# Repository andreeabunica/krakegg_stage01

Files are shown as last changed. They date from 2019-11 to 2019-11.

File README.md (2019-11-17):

# krakegg_stage01
Krakegg is a soft robotics end effector exploring the implementation of bionic actuation for soft robotics grippers. The repository is documenting the first stage of development. 

The repository contains the files, code & hardware components used in the first prototype of the project.

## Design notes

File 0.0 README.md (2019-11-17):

# krakegg_stage01
Krakegg is a soft robotics end effector exploring the implementation of bionic actuation for soft robotics grippers. The repository is documenting the first stage of development. 

The repository contains the files, code & hardware components used in the first prototype of the project. 

In the documents, you will find: 

  A. Text instructions: 

0.Concept & process: explaining the overall process leading to the development of the Stage 1 Prototype for the soft robotics gripper. 

0_01: Bill of materials: a list of the materials used for the production for the Stage 1 Prototype, with affiliated links to similar products that can be purchased from Amazon/ local retailers. 

0_02: Build process: documenting the steps taken in order to build the Stage 1 Prototype

  B. 3D printing files: 

01_Krakegg Stage 01- Moulds_Baked (...): Rhino file of the specific moulds used for the production of the prototype

01_Krakegg Stage 01: Moulds_Parametric (...) : Grasshopper file of the parametrized moulds, in order to quickly change the parameters and generate new 3D printing-ready files 

02_Krakegg Stage 01- Connection to robot arm (...): Rhino file of the current iteration of the connection plate, air chamber and finger holder to the plate

  C. Circuit: 

03_Krakegg Stage 01- Circuit: zipped folder containing hardware circuit information, including wiring instructions

03_Krakegg Stage 01- Arduino code: .ino file containing the current iteration of Arduino code

Prototype demonstration videos: 

- Egg picking demonstration: https://www.youtube.com/watch?v=kh5d-S89E1A&feature=youtu.be

- Force sensor test: https://www.youtube.com/watch?v=OoQZakSipXg&feature=emb_title

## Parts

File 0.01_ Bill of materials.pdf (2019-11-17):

KRAKEGG / Stage 01 Final Prototype Bill of Materials

### 01. SOFT ROBOTICS FINGERS

_3D printed moulds
_casting silicone (Eco-Flex 00-50): https://www.amazon.com/Smooth-Ecoflex-00-50-Platinum-Silicone/dp/B00GJ80HIC_syringe + needle

### 02. CONNECTION TO ROBOTIC ARM

_3D printed connection plate
_bolts
_screws & nuts
_Connector rivets

### 03. HARDWARE

Connection to the robot ( to ABB 140 in this case):
_microcontroller (arduino uno or similar): https://www.amazon.com/RoboGets-Compatible-ATmega328P-Microcontroller-Electronics/dp/B 01N4LP86I (https://www.amazon.com/RoboGets-Compatible-ATmega328P-Microcontroller-Electronics/dp/B01N4LP86I)
_octocoupler:
https://www.amazon.com/Converter-Optocoupler-Isolator-Maluokasa-DST-1R4P-N/dp/B07NNP 4H7S (https://www.amazon.com/Converter-Optocoupler-Isolator-Maluokasa-DST-1R4P-N/dp/B07NNP4H7S/)
_relay:
https://www.amazon.com/Nilight-Automotive-Harness-Interlocking-Socket/dp/B0748F1JK4

Control air pressure:
_2 way solenoid valve:
https://www.amazon.com/4inch-Normally-Closed-Electric-Solenoid/dp/B00ON8XFSO_air compressor:
https://www.amazon.com/AstroAI-Portable-Compressor-Inflator-Protection/dp/B078LYX5YF_force touch sensor:
https://www.amazon.com/Sensitive-Resistor-Pressure-Diameter-Resistance-Type/dp/B07MP4R L9Q (https://www.amazon.com/Sensitive-Resistor-Pressure-Diameter-Resistance-Type/dp/B07MP4RL9Q)

General:
_jumper cables & jumper extension wires: https://www.amazon.com/Elegoo-EL-CP-004-Multicolored-Breadboard-arduino/dp/B01EV70C78_breadboard:
https://www.amazon.es/Protoboard-contactos-Breadboard-prototipos-soldadura/dp/B00JGFDKBQ/ (https://www.amazon.es/Protoboard-contactos-Breadboard-prototipos-soldadura/dp/B00JGFDKBQ)

_12V power supply:
https://www.amazon.com/Switching-Universal-Regulated-Transformer-Computer/dp/B07C2WB R1L (https://www.amazon.com/Switching-Universal-Regulated-Transformer-Computer/dp/B07C2WBR1L)
_Mounting plate or Project Box

Tools:

_Soldering iron
_Wire strippers
_Tweezers
_Screwdriver
_3D printer

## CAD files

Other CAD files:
01_Krakegg Stage 01- Moulds_ Baked Soft robotics Finger.3dm
02_Krakegg Stage 01- Connection to robot arm 3D printing file.3dm

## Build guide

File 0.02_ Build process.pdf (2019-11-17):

KRAKEGG / Stage 01 Final Prototype Build process

### 01. SOFT ROBOTICS FINGERS

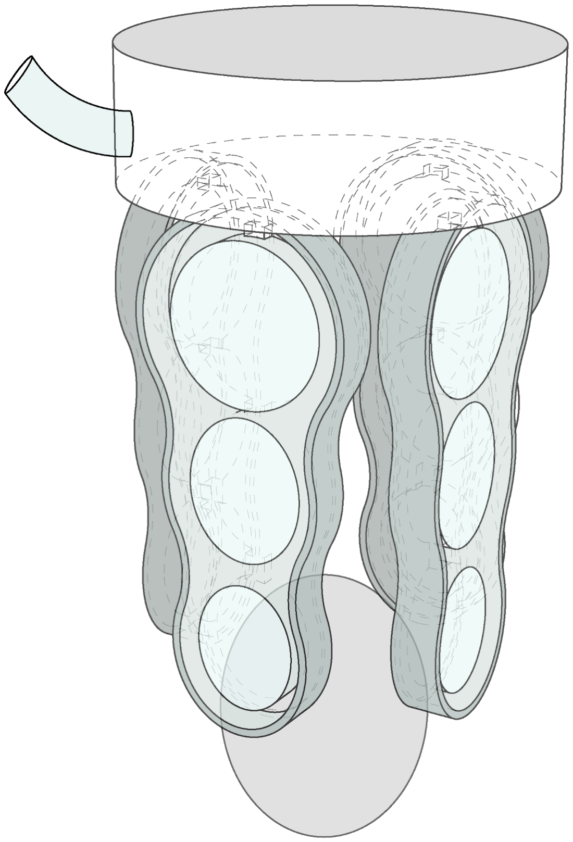
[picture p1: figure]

1. Design your mould using the attached grasshopper file, or download the 3D printing-ready files from the attached Rhino file.

Make sure to add a T-shaped end to the beginning of your air channel in order to later attach the fingers to the robot connection module.

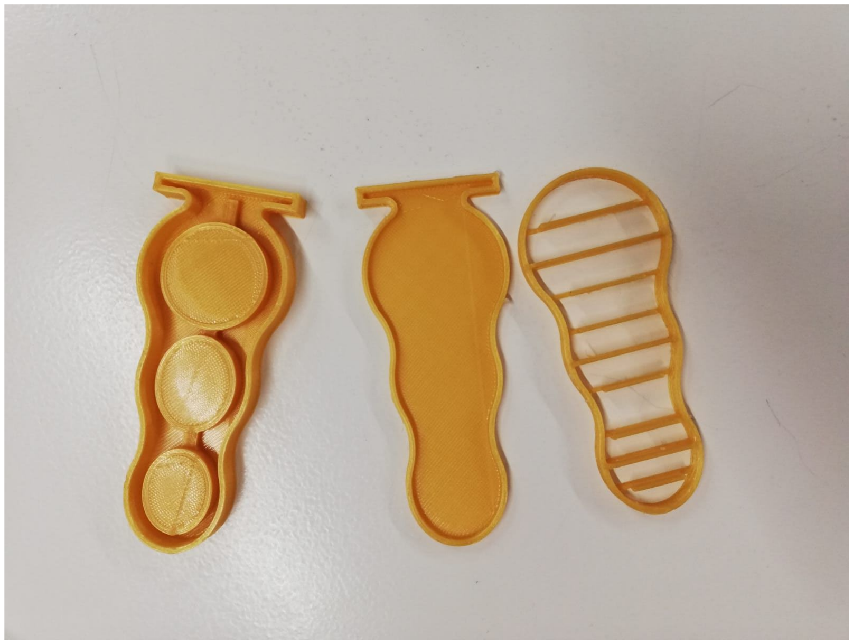
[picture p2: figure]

2. 3D print your mould (photo above)
3. Mix the two parts of Eco-flex 00-50 silicone according to the instructions on the packaging.
4. Pour the silicone in the bottom mould, up to the lip.
5. Pour the silicone in the main body mould, up to the lip. Then, place the spacer mould on top, making sure the indents are sunk in the silicone poured in the main body mould.

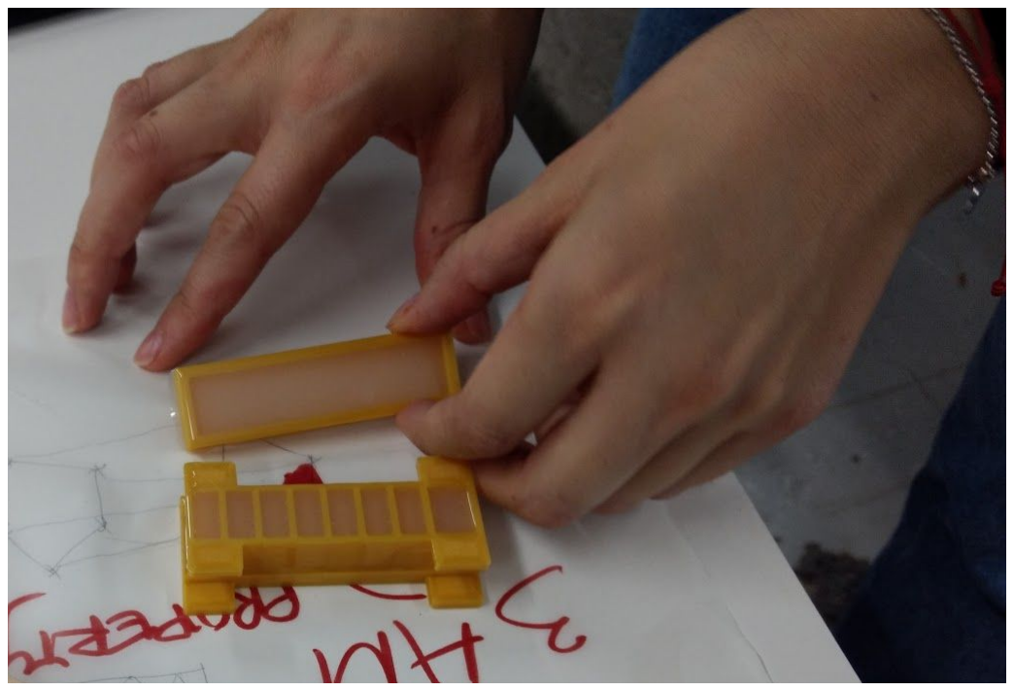
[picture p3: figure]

6. Leave the moulds to dry for at least 2 hours before carefully de-moulding.
7. Glue the bottom mould to the main body mould by applying a thin layer of silicone on the edges of the bottom mould and then placing the main body mould on top. Apply extra silicone on the vertical walls around the seam if needed to tightly close the mould.

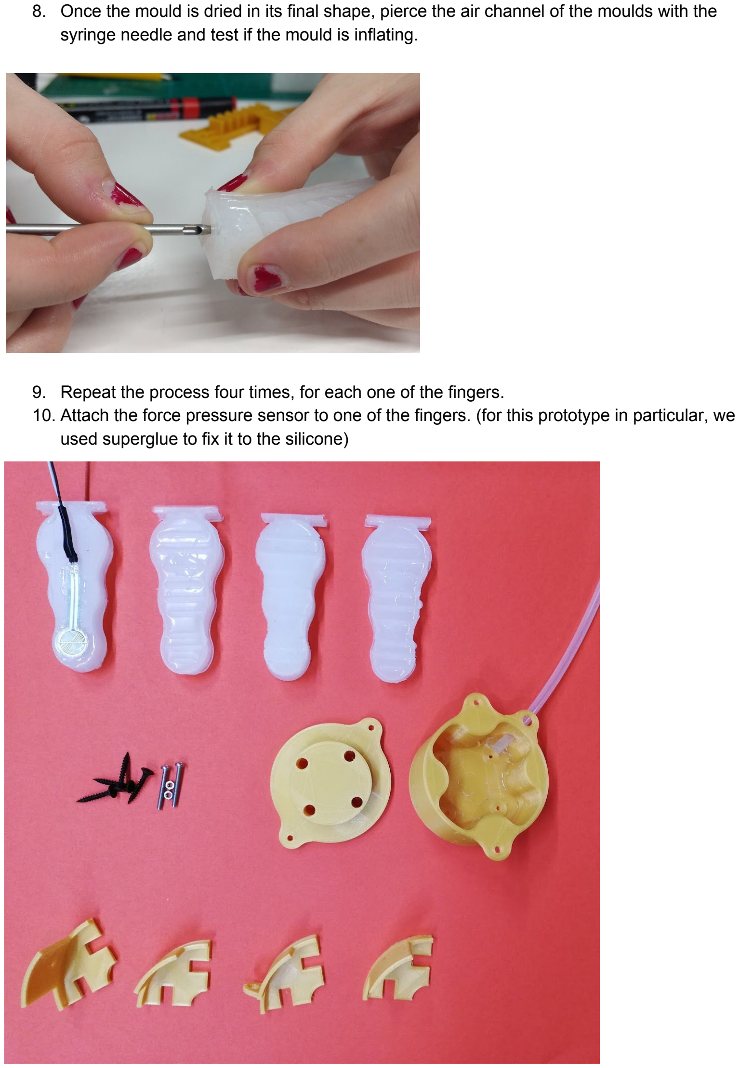
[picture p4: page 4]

8. Once the mould is dried in its final shape, pierce the air channel of the moulds with the syringe needle and test if the mould is inflating.
9. Repeat the process four times, for each one of the fingers.
10. Attach the force pressure sensor to one of the fingers. (for this prototype in particular, we used superglue to fix it to the silicone)

### 02. CONNECTION TO ROBOTIC ARM

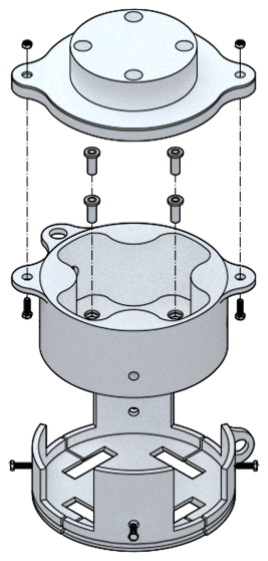
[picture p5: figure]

1. Download the Rhino file for the robot arm connection and 3D print it.
2. First screw in the robot arm connection plate using bolts compatible to the specific robot arm you are working with
3. Glue in the air inputs to the fingers to the bottom of the air chamber. (In this case we used four cut-up aluminium rivets as air inputs)
4. Fix each finger in between the finger holder plates and connect each one of them to one of the air inputs.
5. Fix the air chamber to the robot connection plate using screws and washers. (In this case we ended up cutting up a rubber plate in the shape of the connection plate and placing it in between the air chamber and the connection plate in order to reduce the amount of air leakage)
6. Fix the finger holders and the fingers to the rest of the connection module using screws.

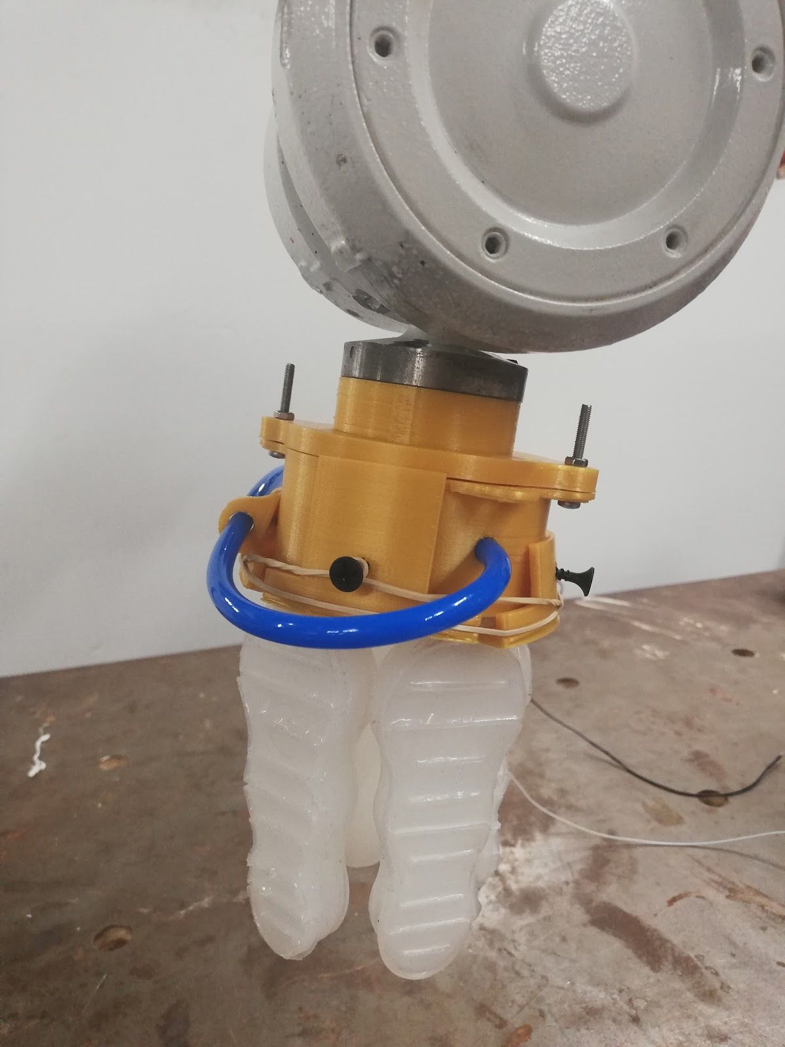
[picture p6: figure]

* This prototype
also used electrical
tape and elastic
bands as an extra
sealing layer to
reduce air leakage
to workable levels

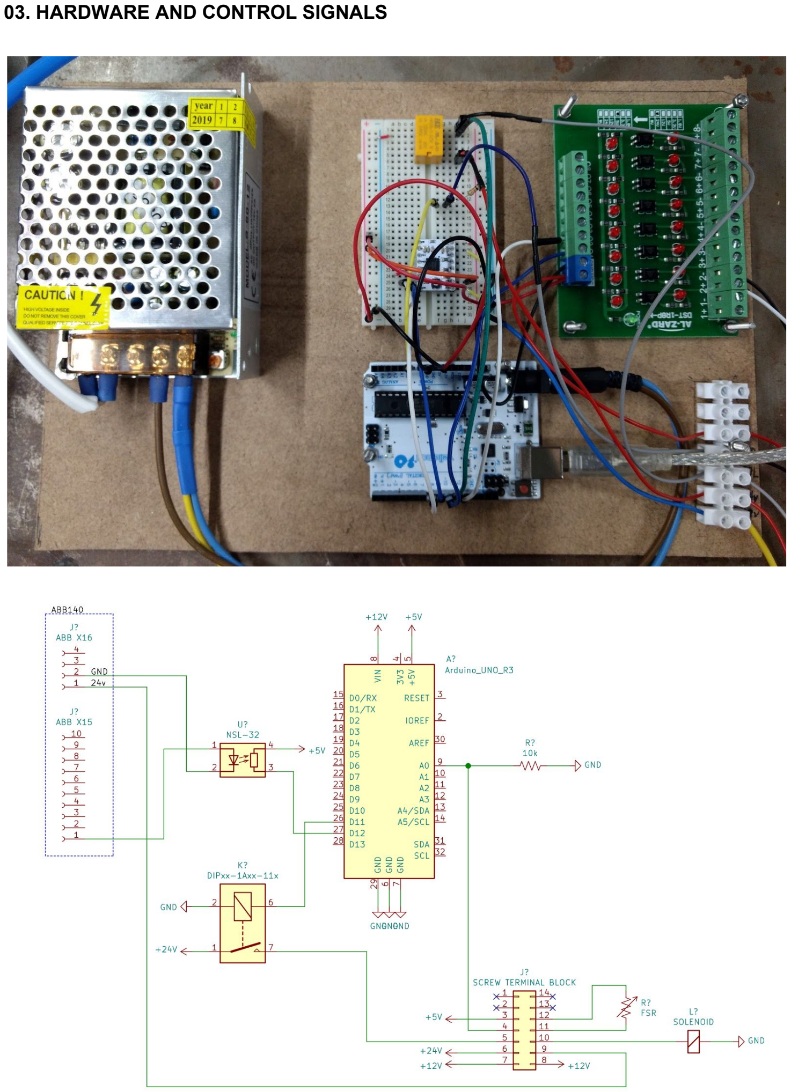
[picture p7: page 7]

### 03. HARDWARE AND CONTROL SIGNALS

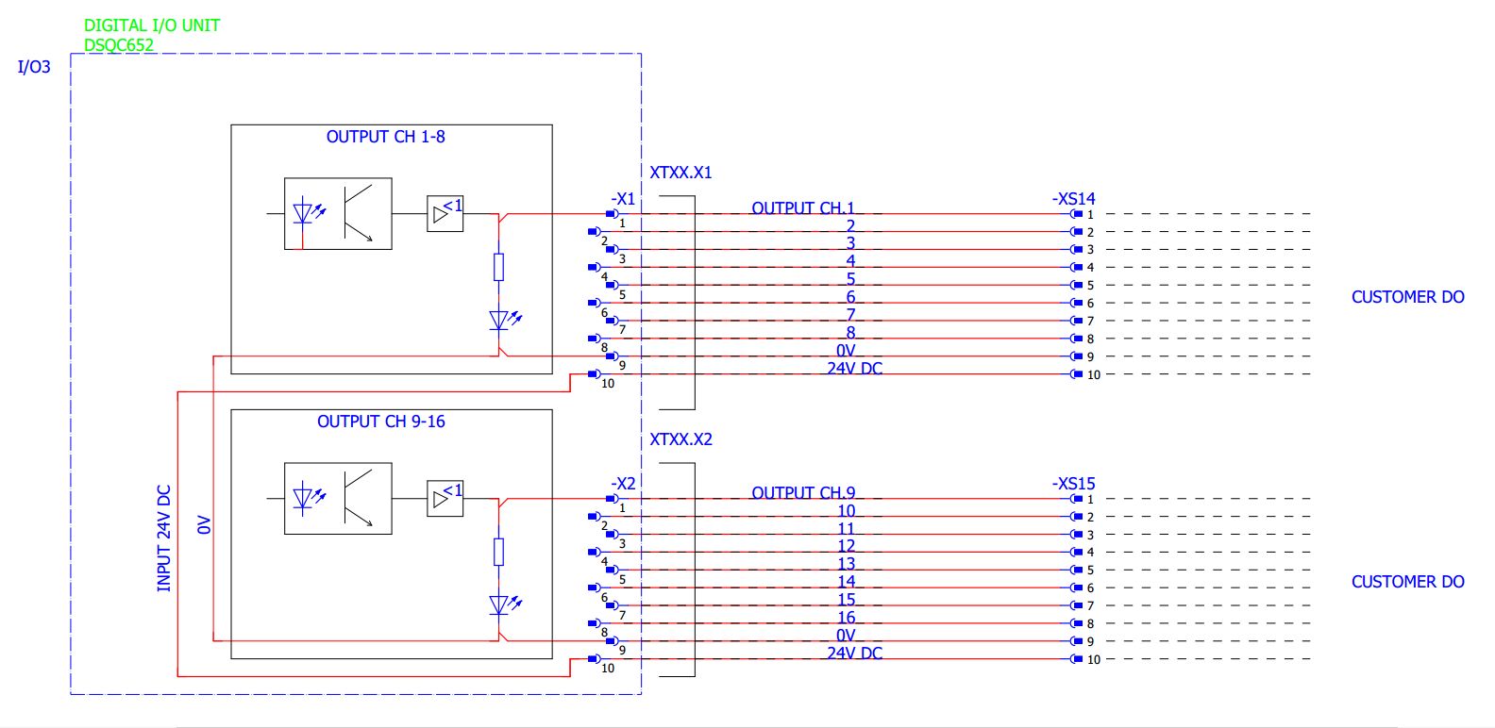
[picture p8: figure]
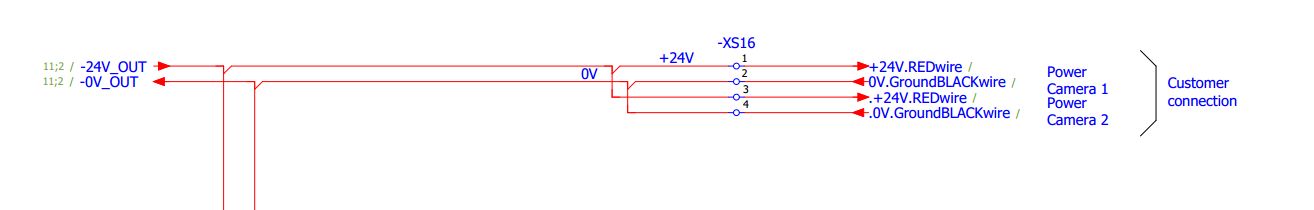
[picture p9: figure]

1. First, the robot sends signals from its digital IO’s. This prototype used an ABB IR140, using the X15 and X16 ports for power and signals. (See diagram).
2. The 24v robot DO signal from X15 passes through an optocoupler to provide a 5v signal to the microcontroller. This lets the microcontroller know when the program expects the gripper to be activated.
3. However, the gripper shouldn’t continue to inflate constantly when in this state, so for this prototype a force-sensitive resistor was used to detect when the gripper has made sufficient contact with the workpiece. The microcontroller considers both inputs and sends out a 5v signal. Note : Since the gripper reservoir had an amount of leakage in this prototype, turning off the solenoid will immediately start to deflate the fingers. To keep the solenoid from ‘bouncing’ rapidly when the force hovers around the cutoff point, the timing of changes is monitored, and the solenoid will only switch every 250ms at minimum. This feature will become unnecessary with the inclusion of a tighter seal and controllable deflation.
4. The microcontroller output signal passes through a relay which switches the 24v supply from X16 on the robot. This signal then connects to the air solenoid to send air to the gripper.

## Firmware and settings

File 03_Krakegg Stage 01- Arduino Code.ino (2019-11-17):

#define PIN_RELAY 11
#define PIN_ROBOT 12
#define PIN_LIGHT 13
#define PIN_FSR   A0

boolean relayState = false;
uint32_t lastChange = -1;
boolean lastState = false;

void setup() {
  Serial.begin(9600);
  pinMode(PIN_ROBOT, INPUT);
  pinMode(PIN_RELAY, OUTPUT);
  pinMode(PIN_LIGHT, OUTPUT);
  pinMode(PIN_FSR, INPUT);
}


void loop() {
  boolean robotSignal = !digitalRead(PIN_ROBOT);

  boolean relayState  = robotSignal;

  float sensorValue = analogRead(PIN_FSR);
//  Serial.println(sensorValue);
  if (sensorValue > 512) {
    relayState = false;
  }

  if (relayState != lastState) {
    // Debounce, only allow a change every 250ms
    if (millis() - lastChange < 250) {
      relayState = lastState;
    }
    else {
      lastState = relayState;
      lastChange = millis();
    }
  }

  digitalWrite(PIN_RELAY, relayState);
  digitalWrite(PIN_LIGHT, relayState);
}
